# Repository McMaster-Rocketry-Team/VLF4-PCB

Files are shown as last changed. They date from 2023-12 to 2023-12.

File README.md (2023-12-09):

# Void Lake Fusion 4 (VLF4)

SRAD Avionics from the [McMaster Rocketry Team](https://www.macrocketry.ca/)

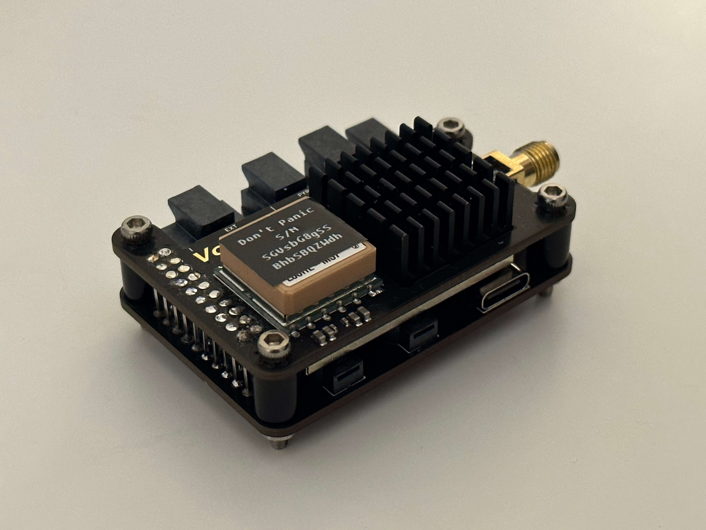
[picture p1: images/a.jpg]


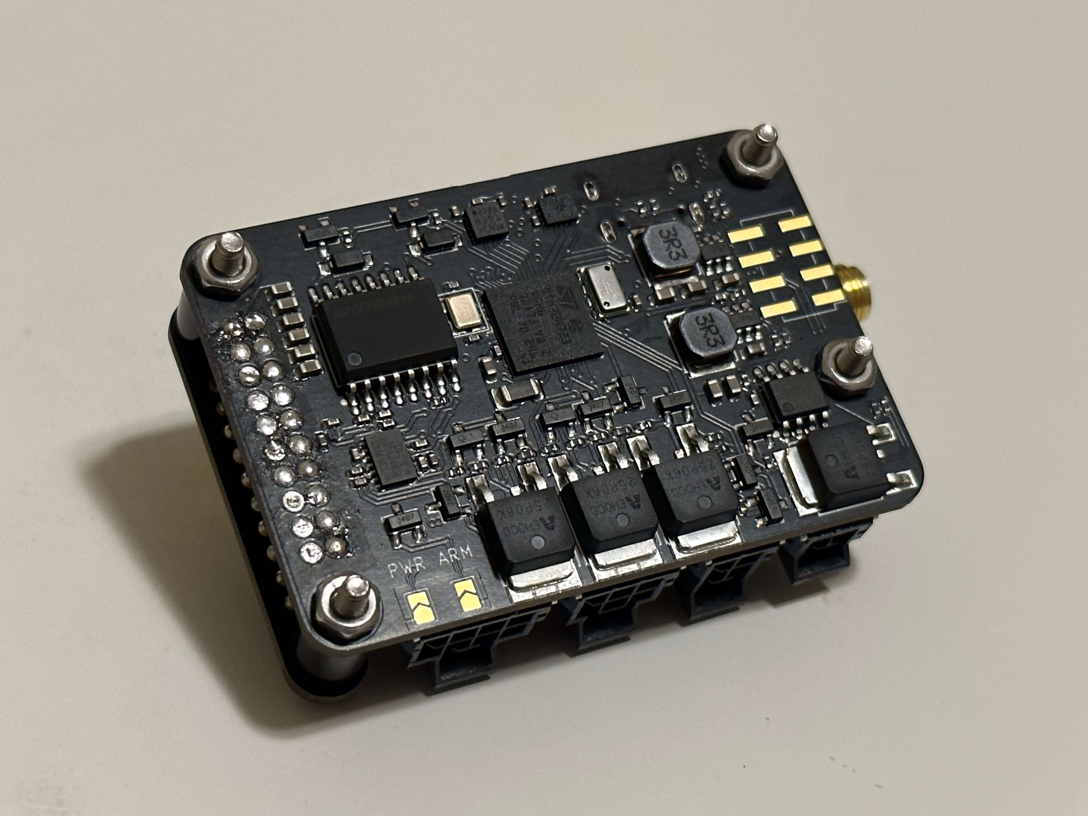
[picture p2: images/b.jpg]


[Our Avionics Museum](https://mcmasterrocketry.notion.site/Void-Lake-Museum-7bf3bac829b94e0fac715c41c5d70cb9)

## Selling point

- Pyro short circuit protection
- Molex nano-fit connectors
- 1W LoRa, 100km+ LoS range
- GPS + IMU + baro sensor fusion, reducing the chance of ejecting prematurely
- Modern 3D visualizer
- Small
- Open source firmware
- Relatively cheap

## Pyro
- 3 pyro channels, each 8A continuous (current limited by the connector due to size)
- pyro channels not connected to battery+ when not firing (unlike raven)
- continuity detection
- short circuit protection

## Sensors
- MCU: STM32H723
- IMU 1: ±2000deg/s ±16g (LSM6DSMTR)
- IMU 2: ±100g (H3LIS100DLTR)
- Magnetometer: MMC5603NJ
- Barometer: max altitude 30km (MS5607)
- Storage: 64MB NOR Flash (W25Q512JVFIQ)
- GPS: L80RE-M37
- Radio: 1W LoRa (e22-900m30s)

## Connectivity
- 2 buzzers for stereo sound
- usb type-c
- battery: 2 pin molex nano-fit
- power & arming switch: 4 pin molex nano-fit (no large current is carried over switches)
- pyro: 6 pin molex nano-fit
- extension: 8 pin molex nano-fit:
  - ground: 1 pin
  - power out (battery voltage) (only provides power out if the power switch is turned on): 1 pin
  - serial: 2 pins
  - CAN: 2 pins
  - GPIO: 2 pins
- Serial Wire Debug: 5 pin molex pico-clasp
- SMA antenna connector

## Software (WIP, to be open sourced)
- Async embedded rust

## JLCPCB Manufacturing Specifications

- Base Material: FR-4
- Layers: 6
- PCB Thickness: 1.6
- **Impedance Control: yes JLC06161H-3313**
- PCB Color: Black
- Silkscreen: White
- Material Type: FR-4 TG155

- **Via Covering: Epoxy Filled & Capped**
- Surface Finish: ENIG
- Gold Thickness: 1 U"
- Deburring/Edge rounding: No
- Outer Copper Weight: 1 oz
- Inner Copper Weight: 0.5 oz
- Gold Fingers: No
- Flying Probe Test: Fully Test
- Castellated Holes: no
- Remove Order Number: Specify a location
- **Min via hole size/diameter: 0.2mm/(0.3/0.35mm)**
- 4-Wire Kelvin Test: Yes
- Paper between PCBs: No
- Appearance Quality: IPC Class 2 Standard
- Confirm Production file: Yes
- Silkscreen Technology: Ink-jet/Screen Printing Silkscreen
- X-out board: Accept
- Package Box: With JLCPCB logo
- Board Outline Tolerance: ±0.2mm(Regular)

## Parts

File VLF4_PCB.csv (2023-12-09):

# | Reference | Qty | Value | Footprint | DNP
1 | BUZZER1, BUZZER2 | 2 | MLT-9032 | Rocketry:BUZ-SMD_MLT-9032
2 | C1, C2, C7, C10, C11, C12, C13, C14, C15, C17, C18, C19, C20, C21, C22, C24, C27, C31, C34, C36, C37, C39, C41, C42, C43 | 25 | 100n | Capacitor_SMD:C_0402_1005Metric
3 | C3, C4, C8, C9, C51, C52, C53, C54, C55, C56, C57, C58, C59 | 13 | 22u | Capacitor_SMD:C_0603_1608Metric
4 | C5, C6, C25, C35, C38, C40 | 6 | 10u | Capacitor_SMD:C_0603_1608Metric
5 | C16, C26, C30, C46, C47, C48, C49, C50 | 8 | 1u | Capacitor_SMD:C_0402_1005Metric
6 | C23 | 1 | 4.7u | Capacitor_SMD:C_0402_1005Metric
7 | C28, C29 | 2 | 2.2uL | Capacitor_SMD:C_0402_1005Metric
8 | C32, C33 | 2 | 10p | Capacitor_SMD:C_0402_1005Metric
9 | C44, C45 | 2 | 100p | Capacitor_SMD:C_0402_1005Metric
10 | D1, D2, D3, D4 | 4 | B5819W_C8598 | Rocketry:SOD-123_L2.7-W1.6-LS3.7-RD-1
11 | D5 | 1 | MMBZ27VCLT1G-N | Package_TO_SOT_SMD:SOT-23
12 | H1, H2, H3, H4, H5, H6, H7, H8 | 8 | MountingHole | Rocketry:MountingHole_2.7mm_M2.5_Keepout
13 | HS1 | 1 | Heatsink | Rocketry:heatsink_20x20x10
14 | J1, J2 | 2 | Conn_02x10_Odd_Even | Rocketry:02x10_Compact_Connector
15 | J_BAT1 | 1 | Conn_01x02 | Molex:1054301102
16 | J_EXT1 | 1 | Conn_02x04_Top_Bottom | Molex:1054051108
17 | J_EXT2 | 1 | Conn_02x04_Top_Bottom | Connector_PinHeader_2.54mm:PinHeader_2x04_P2.54mm_Vertical_SMD
18 | J_PYRO1 | 1 | Conn_02x03_Top_Bottom | Molex:1054051106
19 | J_SW1 | 1 | Conn_02x02_Top_Bottom | Molex:1054051104
20 | JP1, JP2 | 2 | SolderJumper_2_Open | Jumper:SolderJumper-2_P1.3mm_Open_TrianglePad1.0x1.5mm
21 | L1, L2 | 2 | FNR5020S3R3NT | Rocketry:IND-SMD_L5.0-W5.0_FNR50XXS
22 | L3 | 1 | 3.3uh | Inductor_SMD:L_1206_3216Metric
23 | LED1 | 1 | 19-217/BHC-ZL1M2RY/3T | Rocketry:LED0603-FD_BLUE
24 | LED_G1 | 1 | 19-217/GHC-YR1S2/3T | Rocketry:LED0603-RD
25 | LED_R1 | 1 | KT-0603R | Rocketry:LED0603-RD
26 | Q1, Q4, Q10, Q14 | 4 | AP25P06K | Rocketry:TO-252-2_L6.6-W6.1-P4.57-LS10.1-BL
27 | Q2, Q3, Q5, Q7, Q8, Q11, Q12, Q15 | 8 | CJ3407 | Rocketry:SOT-23-3_L2.9-W1.6-P1.90-LS2.8-BR
28 | Q6, Q9, Q13, Q16, Q17 | 5 | MMBT5551_C2145 | Rocketry:SOT-23-3_L2.9-W1.3-P1.90-LS2.4-BR
29 | Q18, Q19, Q20 | 3 | 2N7002 | Rocketry:SOT-23-3_L2.9-W1.3-P1.90-LS2.4-BR
30 | R1 | 1 | 3.9K | Resistor_SMD:R_0402_1005Metric
31 | R2 | 1 | 20K | Resistor_SMD:R_0402_1005Metric
32 | R3, R10, R12, R14, R16, R18, R20, R22, R27, R29, R30, R31 | 12 | 33K | Resistor_SMD:R_0402_1005Metric
33 | R4, R7, R11, R15, R19 | 5 | 10K | Resistor_SMD:R_0402_1005Metric
34 | R5 | 1 | 27K | Resistor_SMD:R_0402_1005Metric
35 | R6 | 1 | 3.3K | Resistor_SMD:R_0402_1005Metric
36 | R8 | 1 | 56K | Resistor_SMD:R_0402_1005Metric
37 | R9 | 1 | 200R | Resistor_SMD:R_0402_1005Metric
38 | R13, R17, R21 | 3 | 510R | Resistor_SMD:R_0402_1005Metric
39 | R23, R24 | 2 | 330R | Resistor_SMD:R_0402_1005Metric
40 | R25, R26 | 2 | 5.1K | Resistor_SMD:R_0402_1005Metric
41 | R28 | 1 | 75R | Resistor_SMD:R_0402_1005Metric
42 | R32 | 1 | 33R | Resistor_SMD:R_0402_1005Metric
43 | RF1 | 1 | BWSMA-KE-P001 | Rocketry:SMA-SMD_BWSMA-KE-P001
44 | SWD1 | 1 | 532610571 | Rocketry:CONN-SMD_5P-P1.25_532610571-2
45 | U1 | 1 | CC6920SO-30A | Rocketry:SOP-8_L4.9-W3.9-P1.27-LS6.0-BL
46 | U2, U3 | 2 | AP62300TWU | Package_TO_SOT_SMD:TSOT-23-6
47 | U4 | 1 | W25Q512JVFIQ | Rocketry:SOIC-16_L10.3-W7.5-P1.27-LS10.4-BL
48 | U5 | 1 | MS560702BA03-50 | Rocketry:SENSOR-SMD_MS560702BA03-50
49 | U6 | 1 | H3LIS100DLTR | Rocketry:TFLGA-16_L3.0-W3.0-P0.50-TL
50 | U7 | 1 | MMC5603NJ | Rocketry:FLIPCHIP-4_L0.8-W0.8-R2-C2-P0.40-TL
51 | U8 | 1 | LSM6DSMTR | Rocketry:LGA-14_L3.0-W2.5-P0.50-TL
52 | U9 | 1 | STM32H723VGHx | Package_BGA:TFBGA-100_8x8mm_Layout10x10_P0.8mm
53 | U10 | 1 | L80RE | Rocketry:GPSM-SMD_12P-L16.0-W16.0-P2.54-BL
54 | U11 | 1 | E22-900M30S | Rocketry:WIRELM-SMD_E22-900M30S
55 | U12 | 1 | TJA1043TK/1Y | Rocketry:HVSON-14_L4.5-W3.0-P0.65-BL-EP
56 | USB1 | 1 | TYPEC-304J-BCP16 | Rocketry:USB-C-SMD_TYPEC-304J-BCP16
57 | X1 | 1 | X322516MLB4SI | Rocketry:OSC-SMD_4P-L3.2-W2.5-BL

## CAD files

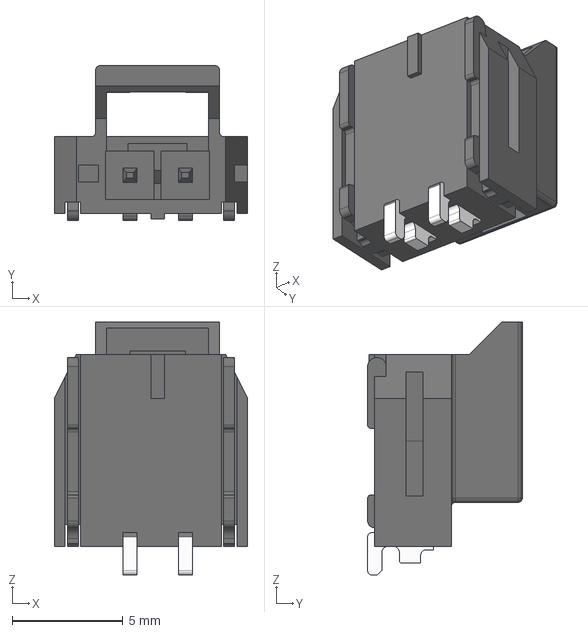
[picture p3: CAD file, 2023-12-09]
components/extern/3dmodels/Molex/1054301102.step
8.74 x 6.99 x 11.4 mm

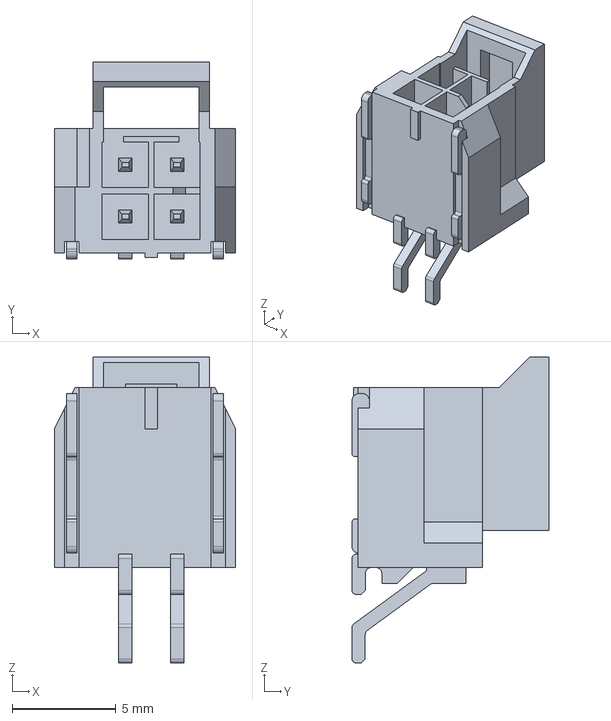
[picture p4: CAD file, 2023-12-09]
components/extern/tmp/1054051104/1054051104.step
8.74 x 9.49 x 14.7 mm

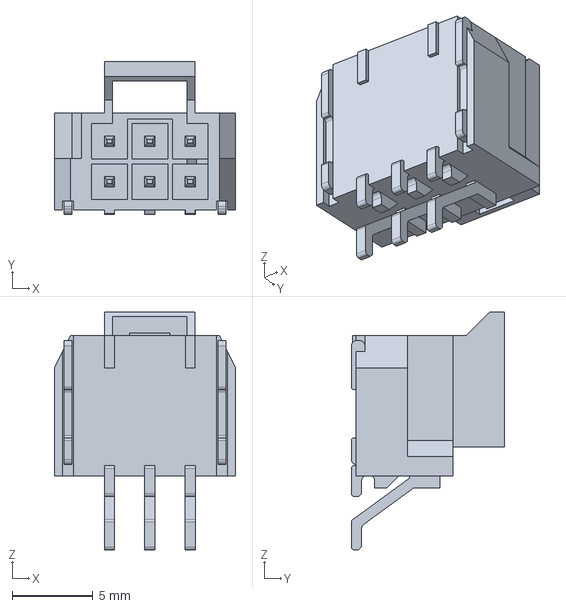
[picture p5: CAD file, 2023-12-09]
components/extern/tmp/1054051106/1054051106.step
11.2 x 9.49 x 14.7 mm

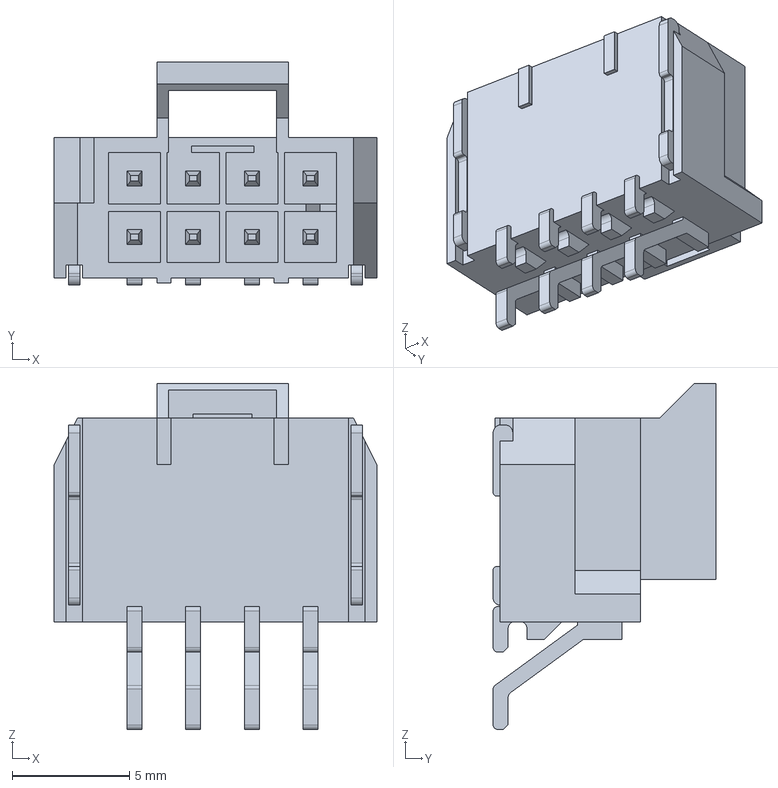
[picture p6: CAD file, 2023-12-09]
components/extern/tmp/1054051108/1054051108.step
13.7 x 9.49 x 14.7 mm

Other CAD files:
components/extern/tmp/1054301102/1054301102.step
components/extern/3dmodels/Molex/1054051108.step
components/extern/3dmodels/Molex/1054051104.step
components/extern/3dmodels/Molex/1054051106.step
